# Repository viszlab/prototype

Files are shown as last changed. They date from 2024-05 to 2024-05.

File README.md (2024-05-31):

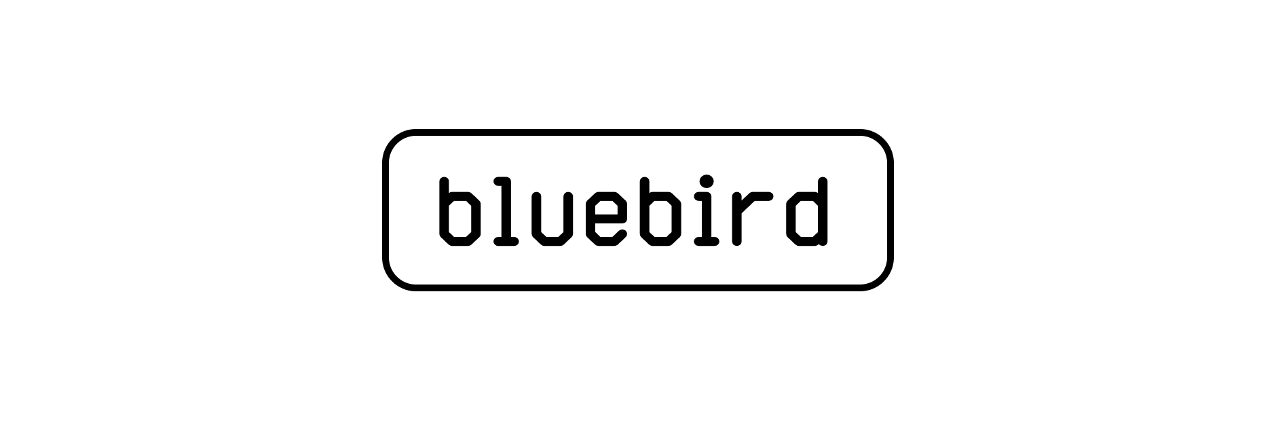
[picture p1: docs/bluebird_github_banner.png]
Bluebird
# 

Bluebird is a [hanging kinetic sculpture](https://en.wikipedia.org/wiki/Kinetic_art) inspired by organic natural materials and the shapes of hanging planters with strings that encode the environmental properties of Indoor Air Quality (IAQ) data in the form of a [data physicalization](http://dataphys.org/). It is meant to be hung from the ceiling in small to medium rooms and changes based on real-time air quality monitor data. Strings (plant branches) either become longer or smaller simulating the growth of a plant and the history and predictions of CO2 concentrations. Movements of the leaves indicate the freshness of air for a multi-sensory experience. The overall design philosophy of the shapes and forms uses the notion of calm technology to convey data with [minimal interruption cost](https://calmtech.com/).

## Components

### Controller
A controller device running on an [Arduino Uno Rev3](https://store.arduino.cc/products/arduino-uno-rev3) microcontroller with a [16-Channel PWM/Servo Shield](https://www.adafruit.com/product/1411) is used to control six [360° MG90S type Micro Servo Motors](https://www.towerpro.com.tw/product/mg90s-3/). Attached to these motors are pulleys with fishing lines simulating the growth of the hanging planter so that the string can be moved up and down.

### Gateway
A gateway device running on a [NodeMCU](https://www.nodemcu.com/index_en.html) (ESP8266-based) microcontroller through wi-fi [IOTroam](https://www.surf.nl/en/services/iotroam) fetches the [Lab42 building API](https://lab42.uva.nl/) to gather the latest real-time CO2 concentrations through the avaliable in-building sensors and sends them over [UART](https://docs.arduino.cc/learn/communication/uart/) to the controller device moving the servo motors.

### Materials
The strings, leaves, and housings of the electronics and mechanical hardware are created using [additive manufacturing](https://en.wikipedia.org/wiki/3D_printing) (3D Printing) using a Fused deposition Modeling (FDM) technique using [Polylactic acid](https://en.wikipedia.org/wiki/Polylactic_acid) (PLA) plastic filament in various colors. The electronics enclosures and plant models were modeled using [computer-aided design](https://en.wikipedia.org/wiki/Computer-aided_design) (CAD) software.

## Installation

1) Install a code editor such as [VSCode](https://vscode.dev/)
2) Install the [PlatformIO extension](https://platformio.org/platformio-ide) for VSCode.
3) Clone this repository to your local machine.

```zsh
$ git clone git@github.com:viszlab/prototype.git
```
4) Create a `config.h` file within the _include_ folder with the WiFi SSID, WiFI Password and Lab42 API credentials.

```c++
/* Wi-Fi credentials to connect to accesspoint */
#define WIFI_SSID "SSID"
#define WIFI_PASSWORD "PASSWORD"

/* Lab42 Building API access credentials */
#define API_URL "URL"
#define API_ENDPOINT "ENDPOINT"
#define ROOM_ID "NUMBER"
#define API_USERNAME "USERNAME"
#define API_PASSWORD "PASSWORD"
```
5) Build and upload the `controller.cpp` to the Arduino UNO
6) Build and upload the `gateway.cpp` to the NodeMCU

## Wiring Diagram

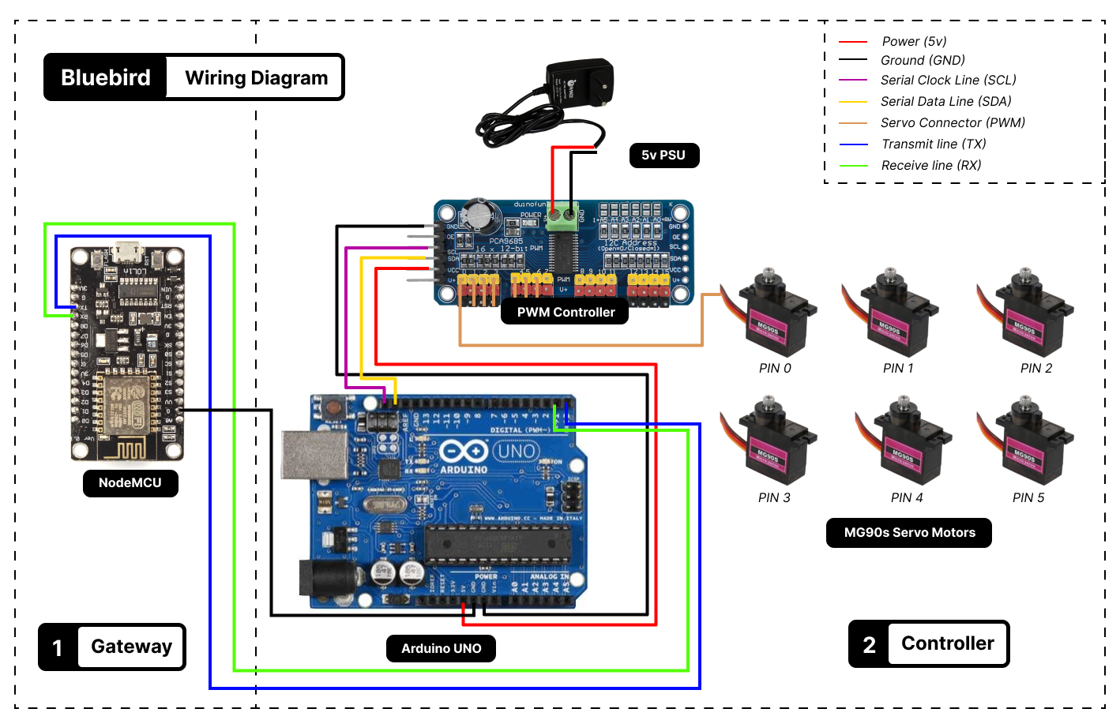
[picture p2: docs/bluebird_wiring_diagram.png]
Wire diagram


## Project structure

```
├── .vscode                 # Platform IO configuration build files
├── docs                    # Documentation files and images
├── models                  # .stl files for the 3D models
├── include                 # Platform IO include dependencies
│   └── config.h            # WiFi and API credentials (.env)
├── lib                     # Arduino custom libraries
├── src                     # Platform IO include dependencies
│   ├── gateway.cpp         # Firmware for the NodeMCU gateway
│   └── controller.cpp      # FIrmware for the Arduino controller
├── test                    # Testing scripts
└── platformio.ini          # Platform IO environment config file
```

## Bill of materials

### Electronics

| Qty | Item |
|-----|---|
| 1x  | **Arduino Uno (Rev3) Atmega328P microcontroller** |
| 1x  | **16-channel I2C PWM-Servo Controller (PCA9685)** |
| 1x  | **Universal 5W 2A DC Power Supply Adapter** |
| 1x  | **NodeMCU (ESP8266-based) microcontroller** |
| 6x  | **Mini Servo (MG90S) Digital (360 continuous degrees)** |

### Cables

| Qty | Item |
|-----|---|
| 4x  | **Jumper Wire female/male (Dupont Style 22AWG)** |
| 6x  | **1000mm RC Servo Extension Cables (Dupont Style)** |

### Hardware

| Qty | Item |
|-----|---|
| 6x  | **M2.5L25 DIN 965 countersunk phillips head screws** |
| 12x | **M2.5L25 DIN 965 countersunk phillips head screws** |
| 12x | **M2.5 Heat set Inserts (OD 5mm, L5mm)** |

### Materials

| Qty | Item |
|-----|---|
| 1x  | **Spool of Greenish color (at least ~270g) of 1.75mm PLA (leaves)** |
| 1x  | **Spool of Color of Choice (at least ~570g) of 1.75mm PLA (mounting plates)** |
| 1x  | **Wooden MDF (or other wood type) plate (5mm thickness)** |
| 5x  | **String or rope in color of choice in ~80cm in length (max 5mm thickness)** |

### Tools

| Qty | Item |
|-----|---|
| 1x  | **Screwdriver with small to large phillips bit** |
| 1x  | **Soldering Iron preferably with Heat Set Insert tips** |

## Recommended print settings

To increase the strength of the pulleys and mounting plates the following printer slicing settings are recommended:

* Layer Height: **0.24mm**
* Infill Percentage: **50%**
* Infill Pattern: **Gyroid**
* Perimeters: **4**
* Top Layers: **5**
* Bottom Layers: **5**

## References

For the basics of working with servo motors this tutorial from _DroneBot Workshop_ was used:

1. DroneBot Workshop. (n.d.). Servo motors with Arduino. Retrieved May 31, 2024, from https://dronebotworkshop.com/servo-motors-with-arduino/

The models of the leaves are based on this seat of Montsera leaves by user _@TriTri_786325_:

2. Printables. (n.d.). 20 Monstera leaf coaster set [Files]. Retrieved May 31, 2024, from https://www.printables.com/model/831698-20-monstera-leaf-coaster-set/files

The printing parameters used for the leaves are based on these settings by user _@Posix_:

3. Printables. (n.d.). Multiuse flexible fabric [Files]. Retrieved May 31, 2024, from https://www.printables.com/model/88579-multiuse-flexible-fabric/files

## Project

[**Viszlab**](https://wwww.viszlab.github.io) is a tangible physical data visualization for the [Lab42](https://lab42.uva.nl/) building. An interactive experience using environment sensor data to offer Human Building-Interaction. Viszlab is developed as a Thesis and Graduation project for the Master (MSc) Information Studies: [Information Systems](https://www.uva.nl/shared-content/programmas/en/masters/information-studies/information-studies.html) (track) at the [University of Amsterdam](https://www.uva.nl/en) by part-time student [Danny de Vries](https://www.dandevri.es/).

* **Master**: Master Information Studies: Information Systems (track)
* **University**: University of Amsterdam (UvA)
* **Institute**: Informatics Institute
* **Faculty**: Faculty of Science (FNWI)
* **Research Group**: Digital Interactions Lab (DIL)
* **Student**: BSc Danny de Vries (14495643)
* **Supervisor**: Dr. H. (Hamed) Seiied Alavi PhD

[Viszlab](https://www.viszlab.github.io) © 2024 by [Danny de Vries](https://wwww.github.com/dandevri) is licensed under [CC BY-NC-SA 4.0](http://creativecommons.org/licenses/by-nc-sa/4.0/?ref=chooser-v1).

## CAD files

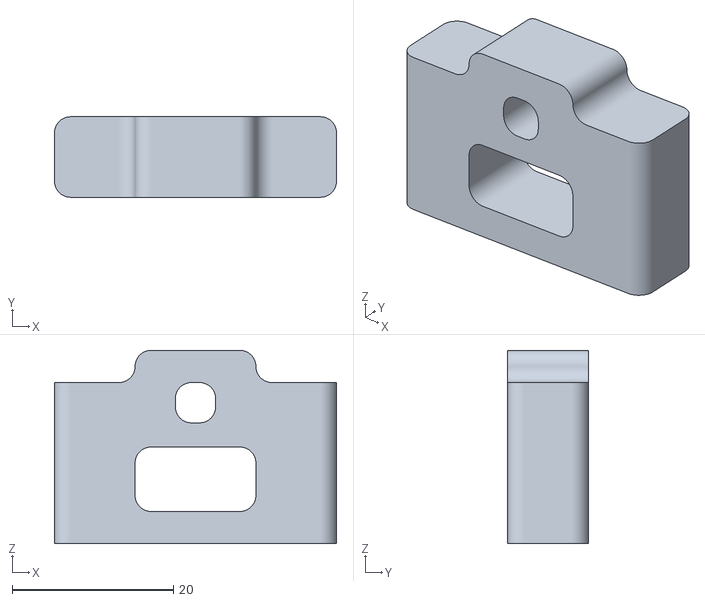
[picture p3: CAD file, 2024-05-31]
models/guide_small_rope.stl
35.0 x 10.0 x 24.0

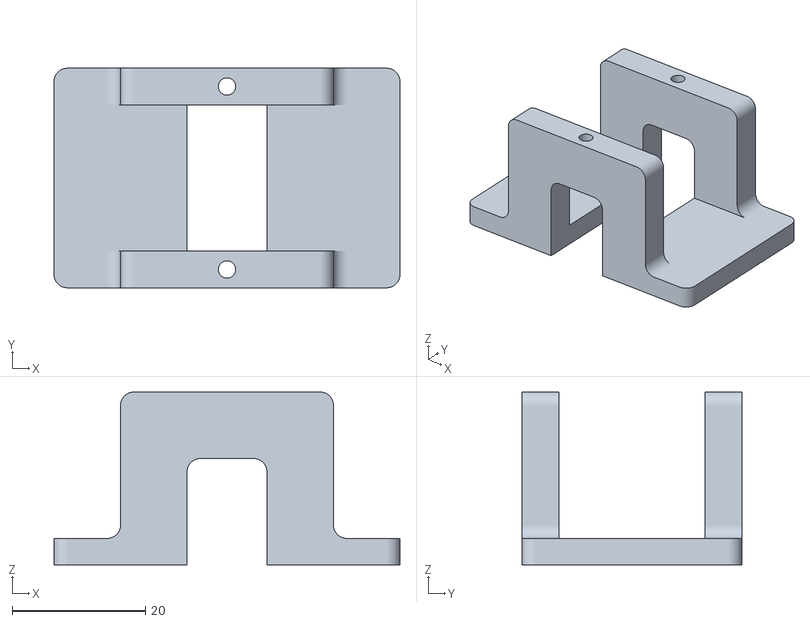
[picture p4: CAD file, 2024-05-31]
models/mount_servo_motor.stl
52.0 x 33.0 x 26.0

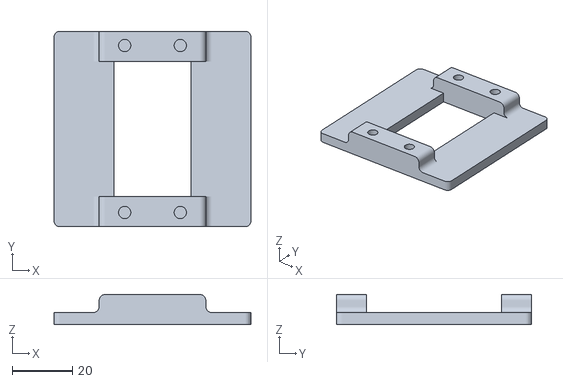
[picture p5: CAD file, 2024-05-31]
models/mount_pca_controller.stl
65.5 x 65.0 x 10.0

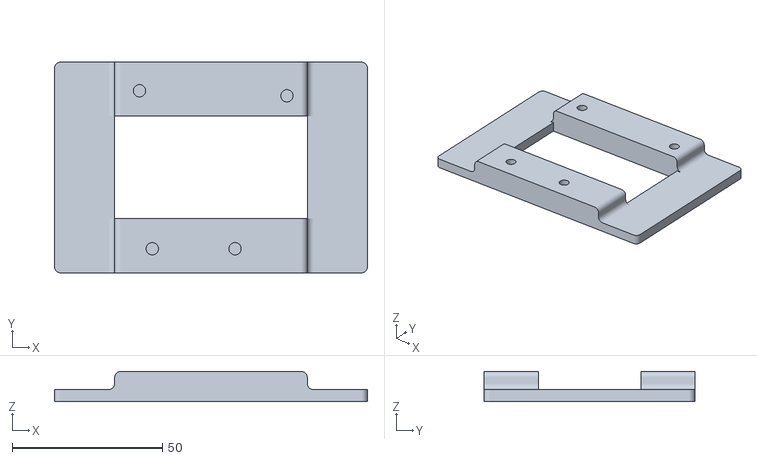
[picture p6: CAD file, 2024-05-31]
models/mount_arduino_uno.stl
104.0 x 70.0 x 10.0

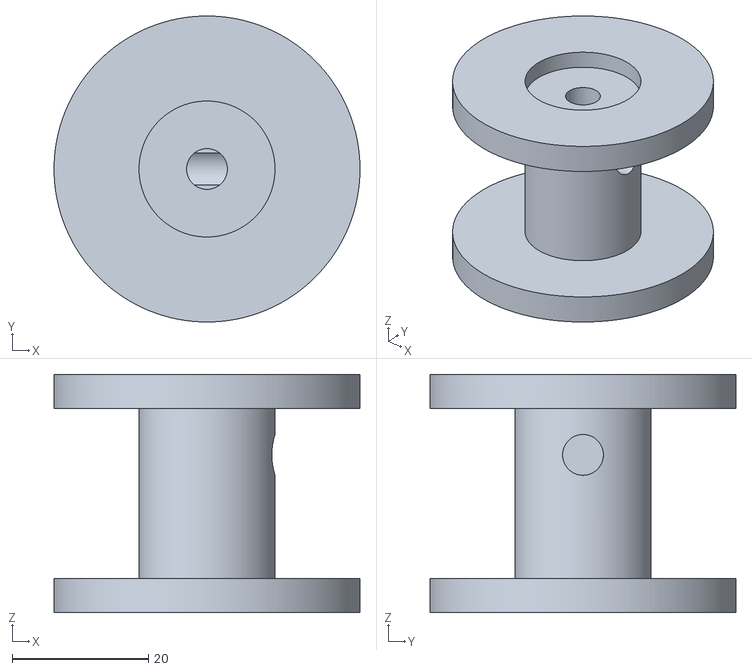
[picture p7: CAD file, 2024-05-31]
models/servo_motor_pulley.stl
45.0 x 45.0 x 35.0

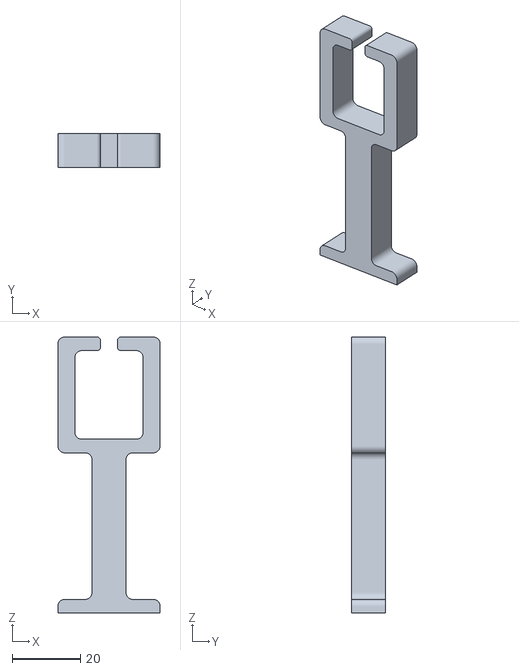
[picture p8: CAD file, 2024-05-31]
models/guide_big_rope.stl
30.0 x 10.0 x 81.0

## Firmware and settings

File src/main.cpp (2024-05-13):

/*

Bluebird data physicalization proof-of-concept.
Controls 4 servo motors using a PCA9685 PWM controller.

---
Master: Master Information Studies: Information Systems (track)
University: University of Amsterdam (UvA)
Institute: Informatics Institute
Faculty: Faculty of Science (FNWI)
Research Group: Digital Interactions Lab (DIL)
Student: BSc Danny de Vries (14495643)
Supervisor: Dr. H. (Hamed) Seiied Alavi PhD
---
*/

/* Include Arduino Framework (built-in) */
#include <Arduino.h>

/* Incude for I2C communications (built-in) */
#include <Wire.h>
#include <SPI.h>

/* Incude PWM library */
#include <Adafruit_PWMServoDriver.h>

/* Set the PWM I2C address (default) */
#define PWM_ADDRESS 0x40

/* PWM frequency for the PCA9685 in Hz */
#define PWM_FREQUENCY 50

/* Connect the servo's on the PWM ports on the board */
#define MOTOR_ONE 0

/* Rotation in milliseconds (speed for rotation and 'growing' factor) */
#define MOVE_TIME 2000

/* Define servo minimum and maximum pulse width in microseconds */
#define SERVO_MIN_PULSE_WIDTH 0
#define SERVO_MAX_PULSE_WIDTH 500

/* Initialize the library with the default PWM address */
Adafruit_PWMServoDriver pwm = Adafruit_PWMServoDriver(PWM_ADDRESS);

/*
  MG90S 360degree continous servo motor pulse widths for rotation
  Figured out by trial and error and changing values.
  Adjust accordingly based on type of servo and manufacturer spec.
  CAVIAT: Have no specified angles like servo motors so wind-up is based on time instead of angle.
 */

#define PULSE_WIDTH_NEUTRAL 325          // Neutral position 'Stops the servo motor'
#define PULSE_WIDTH_CLOCKWISE 311        // Slowest rotation for clockwise
#define PULSE_WIDTH_COUNTERCLOCKWISE 336 // Slowest rotation for counterclockwise

/* Set-up function, only runs on start-up */
void setup()
{

  /* Set the data rate (baud) for serial monitor */
  Serial.begin(9600);

  /* Initialize PWM driver on the specified frequency */
  pwm.begin();
  pwm.setPWMFreq(PWM_FREQUENCY);
}

/* Sets the servo motor pulse width to neutral 'stopping the servo' */
void stopServo(int motorNumber)
{
  pwm.setPWM(motorNumber, 0, PULSE_WIDTH_NEUTRAL);
}

/* Sets the servo motor pulse to move clockwise for 2 seconds 'growing the string' */
void moveClockwise(int motorNumber)
{
  unsigned long startTime = millis(); // Record the start time
  while (millis() - startTime < MOVE_TIME)
  {
    pwm.setPWM(motorNumber, 0, PULSE_WIDTH_CLOCKWISE); // Spin clockwise for 2 seconds
  }
  stopServo(motorNumber);
}

/* Sets the servo motor pulse to move counterclockwise for 2 seconds 'shrinking the string' */
void moveCounterClockwise(int motorNumber)
{
  unsigned long startTime = millis(); // Record the start time
  while (millis() - startTime < MOVE_TIME)
  {
    pwm.setPWM(motorNumber, 0, PULSE_WIDTH_COUNTERCLOCKWISE); // Spin counter clockwise for 2 seconds
  }
  stopServo(motorNumber);
}

void loop()
{
  moveClockwise(0);        // Move clockwise for 2 seconds and stop
  delay(1000);            // Delay for 1 second between movements
  moveCounterClockwise(0); // Move counterclockwise for 2 seconds and stop
  delay(1000);            // Delay for 1 second between movements
}

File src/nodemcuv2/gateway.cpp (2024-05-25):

/*

Title: Wi-fi Gateway for Bluebird data physicaliztaion
Description: Connects to Wi-Fi to fetch CO2 data from the building API and
sends data to Arduino Controller over UART

Hardware: ESP (NodeMCU v3)

---
Master: Master Information Studies: Information Systems (track)
University: University of Amsterdam (UvA)
Institute: Informatics Institute
Faculty: Faculty of Science (FNWI)
Research Group: Digital Interactions Lab (DIL)
Student: BSc Danny de Vries (14495643)
Supervisor: Dr. H. (Hamed) Seiied Alavi PhD
---
*/

/* Include Arduino Framework (built-in) */
#include <Arduino.h>

/* Include Wi-Fi capabilities, HTTP fetches and JSON parsing*/
#include <ESP8266WiFi.h>
#include <ESP8266HTTPClient.h>
#include <ArduinoJson.h>

/* NTP libraries for getting the curent time */
#include <NTPClient.h>
#include <WiFiUdp.h>

/* Establishing the Serial Communication */
#include <SoftwareSerial.h>

/* Stores the wifi-credentials in .env*/
#include <config.h>

WiFiClient wifiClient;
WiFiUDP ntpUDP;
NTPClient timeClient(ntpUDP, "pool.ntp.org", 3600, 60000);

String currentTime; // Global variable to store the current time
String accessToken; // Global variable to store the access token
String endpointRooms;

extern float co2Concentration = 0;


/* Function to send login request */
void sendLoginRequest()
{
  if (WiFi.status() == WL_CONNECTED)
  {
    HTTPClient http;

    http.begin(wifiClient, API_URL);
    http.addHeader("Content-Type", "application/json");

    StaticJsonDocument<200> jsonDoc;
    jsonDoc["username"] = API_USERNAME;
    jsonDoc["password"] = API_PASSWORD;

    String requestBody;
    serializeJson(jsonDoc, requestBody);

    int httpResponseCode = http.POST(requestBody);

    if (httpResponseCode > 0)
    {
      String response = http.getString();
      Serial.println("HTTP Response code: " + String(httpResponseCode));
      Serial.println("Response: " + response);

      // Parse the response to extract the access token
      StaticJsonDocument<200> responseDoc;
      DeserializationError error = deserializeJson(responseDoc, response);

      if (!error)
      {
        accessToken = responseDoc["access_token"].as<String>();
        Serial.println("Access Token: " + accessToken);
      }
      else
      {
        Serial.println("Failed to parse the access token from response");
      }
    }
    else
    {
      Serial.println("Error in sending POST request");
      Serial.println("HTTP Response code: " + String(httpResponseCode));
    }

    http.end();
  }
  else
  {
    Serial.println("Wi-Fi not connected");
  }
}

/* Set-up of the Wi-Fi connection login if succesful and logigng the IP */
void setup()
{
  delay(5000);
  Serial.begin(115200);

  /* Serial BAUD rate for Arduino UNO */
  Serial1.begin(4800); // Serial1 for communication with Arduino Uno (TX and RX pins)

  Serial.println();
  Serial.println("--- Start of set-up ---");

  Serial.println();
  Serial.println("Starting Wi-Fi connection...");

  Serial.print("Connecting to: ");
  Serial.println(WIFI_SSID);

  Serial.println("Connecting to Wi-Fi...");
  WiFi.begin(WIFI_SSID, WIFI_PASSWORD);

  unsigned long startAttemptTime = millis();

  /* Keep attempting to connect until timeout */
  while (WiFi.status() != WL_CONNECTED && millis() - startAttemptTime < 30000)
  {
    Serial.print(".");
    delay(500);
  }

  if (WiFi.status() == WL_CONNECTED)
  {
    Serial.println("Connected to Wi-Fi!");
    Serial.print("IP Address: ");
    Serial.println(WiFi.localIP());

    /* Initialize NTP client */
    timeClient.begin();

    /* Call the function to authenticate */
    sendLoginRequest();
  }
  else
  {
    Serial.print("Wi-Fi connection status: ");
    Serial.println(WiFi.status());
    Serial.println("Failed to connect to Wi-Fi.");
  }

  Serial.println("--- End of set-up ---");
}

void getCurrentTime()
{
  timeClient.update();
  unsigned long epochTime = timeClient.getEpochTime();
  time_t rawTime = epochTime;
  struct tm *ti;
  ti = localtime(&rawTime);

  // Subtract 6 hours because the API formatting is a bit weird?
  ti->tm_hour -= 6;
  if (ti->tm_hour < 0)
  {
    // If the resulting hour is negative, adjust the date
    ti->tm_mday--;     // Move to the previous day
    ti->tm_hour += 24; // Add 24 hours
  }

  // Set seconds to 00 before formatting time string since this is what the API supports
  ti->tm_sec = 0;

  char buffer[30];
  sprintf(buffer, "%02d-%02d-%02d %02d:%02d:%02d", ti->tm_year + 1900, ti->tm_mon + 1, ti->tm_mday, ti->tm_hour, ti->tm_min, ti->tm_sec);
  currentTime = String(buffer);
  endpointRooms = String(API_ENDPOINT) + String(ROOM_ID) + "/data?startTime=" + String{currentTime} + "&endTime=" + String{currentTime};
}

String encodeURL(const String &url)
{
  String encodedURL = "";
  for (int i = 0; i < url.length(); i++)
  {
    if (url[i] == ' ')
    {
      encodedURL += "%20";
    }
    else
    {
      encodedURL += url[i];
    }
  }
  return encodedURL;
}

void sendRequest(const String &endpoint)
{
  if (WiFi.status() == WL_CONNECTED && accessToken.length() > 0)
  {
    HTTPClient http;

    String encodedEndpoint = encodeURL(endpoint);
    http.begin(wifiClient, encodedEndpoint);

    http.addHeader("Content-Type", "application/json");
    http.addHeader("Authorization", "Bearer " + accessToken);

    Serial.println("Access Token: " + accessToken);
    Serial.println("Sending GET request to: " + encodedEndpoint);

    int httpResponseCode = http.GET();

    if (httpResponseCode > 0)
    {
      String response = http.getString();
      Serial.println("HTTP Response code: " + String(httpResponseCode));
      Serial.println("Response: " + response);

      // Parse JSON response
      DynamicJsonDocument jsonDoc(1024); // Set the JSON document size according to your response size
      DeserializationError error = deserializeJson(jsonDoc, response);

      if (!error)
      {
        // Extract CO2 concentration from response and round it to the nearest whole value
        co2Concentration = round(jsonDoc["results"][0]["airquality"].as<float>());
      }
      else
      {
        Serial.println("Failed to parse JSON response");
      }
    }
    else
    {
      Serial.println("Error in sending GET request");
      Serial.println("HTTP Response code: " + String(httpResponseCode));
    }

    http.end();
  }
}

/* Fetches the sensor withing the API room */
void loop()
{

  Serial.println("--- Start of polling (5s intervals) ---");

  getCurrentTime();
  Serial.println("Current Time: " + currentTime);

  Serial.println("API Endpoint: " + endpointRooms);
  sendRequest(endpointRooms);

  Serial.println("CO2 concentrations: ");
  Serial.println(co2Concentration);

  /* Send CO2 concentrations over softserial to Arduino */
  Serial1.println("Hello from NodeMCU");

  Serial.println("--- End of polling (5s intervals) ---");

  delay(5000);
}

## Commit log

2024-01-24 Sample readme.mmd for arduino
2024-04-20 Add platformio init for arduino
2024-05-13 Basic servo motor movement
2024-05-19 Add multi-board platformIO set-up, add gateway API fetch example
2024-05-19 Update readme.md and wiring diagram
2024-05-25 Update gateway to fetch current time and API access token
2024-05-25 Test of UART code
2024-05-31 Update readme.md with printing settings
2024-05-31 Upload .stl files of models
    [guide_big_rope.stl, guide_small_rope.stl, mount_arduino_uno.stl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]
2024-05-31 Update wiring diagram
